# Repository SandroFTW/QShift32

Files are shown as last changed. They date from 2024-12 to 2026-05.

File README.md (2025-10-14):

# QShift32 - ESP32 based timing retard quickshifter module for motorcycles
This project is basically a new revision of my other project "quickshiftuino".
The differences are pretty big though, so I decided to create a new repository.

"**quickshiftuino**" had 2 channels that could cut the power to the ignition coils on the high side (P-Mos).
That topology works great, is fairly simple and reliable, but doesn't allow for more complex features.

"**QShift32**" uses all the thoroughly tested sub-circuits of "quickshiftuino" except the power switching components.
It instead offers 4 independent channels switched by IGBTs on the low side.
They can withstand high voltages and high current and are configured to pull down the low side of the ignition coil.
This can either be used to fully prevent sparks from firing or delay them by a precise time to achieve an ignition retard.

[**Demonstration Video**](https://www.youtube.com/watch?v=TwFzDqyh4EY)

[**Latest feature development: staggered cut**](https://youtu.be/_X9n1uwMxqk)

R1 PCB 3D model:

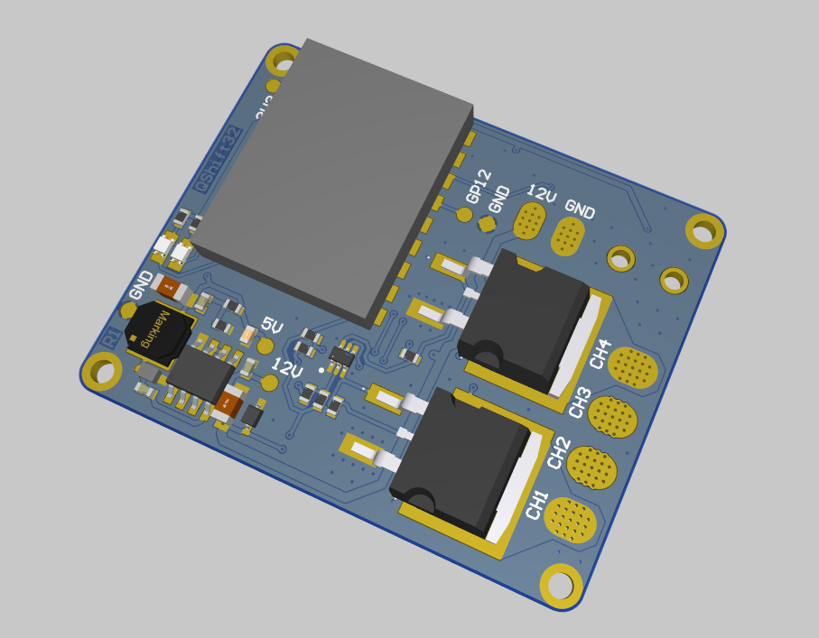
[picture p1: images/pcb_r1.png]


## New possibilities
- Either ignition timing retard or full spark cut to allow clutchless shifting
- Ignition timing retard will smoothly go back to normal operation after shift is done (no jerky movement, less gearbox wear)
- Smooth control over engine power transitions -> extremely smooth shifts (upshifts while leaning and accelerating possible)
- RPM measurement even during power cut (not during full spark cut, only ignition retard)
- During upshift period fuel gets ignited in the exhaust instead of remaining unburnt (controllable pops and flame strength)
- Pit limiter and launch control (RPM limiter) with spark cut and ignition retard (soft limiter or hard limiter with pops and flames)
- Precise dwell time and time per revolution measurement for each channel (1 µs precision)
- Expandable to support handlebar buttons, gear indicator, shift light (not implemented yet), etc.

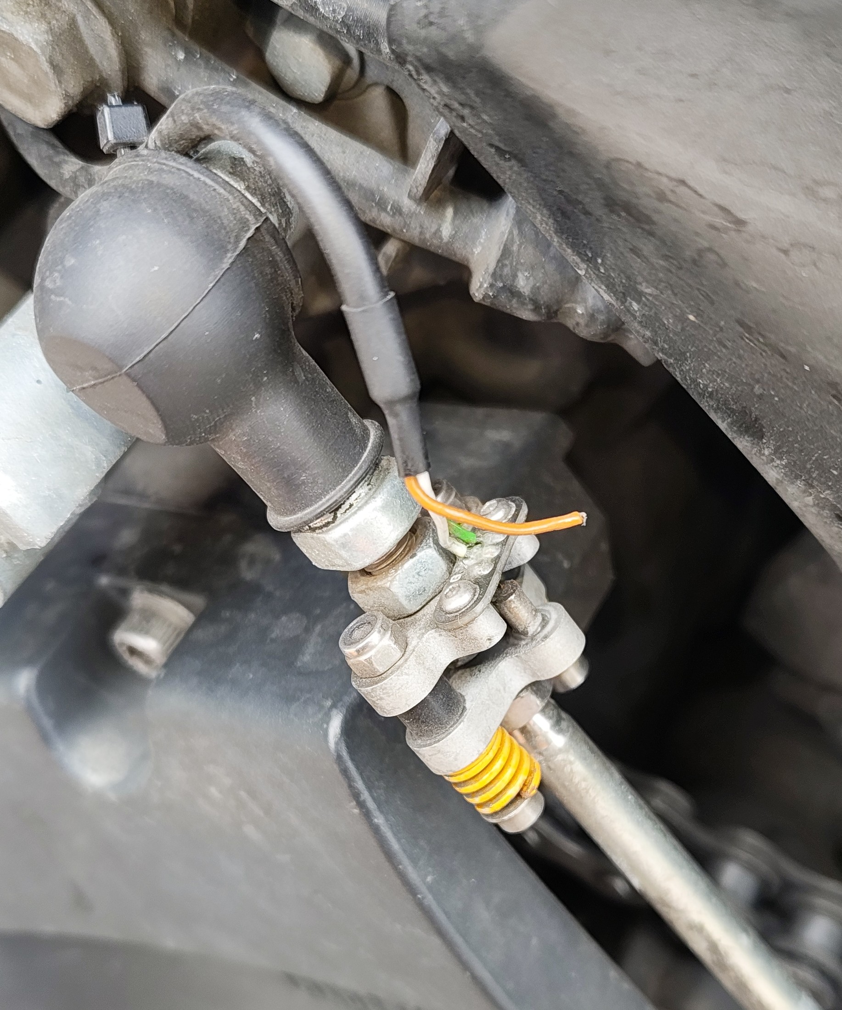
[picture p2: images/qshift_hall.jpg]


My DIY hall based pressure sensor with CNC aluminium parts and 3d printed hotbed springs (die cast springs)
(Ignore the broken wire please ;) )

## Easy configuration
Use any smartphone to connect to the WiFi Access Point opened by QShift32.
IP Adress 192.168.4.1 shows the configuration options.
192.168.4.1/debug.html shows a few internal debug values that can help setting up the config and finding possible errors (mostly needed for development).

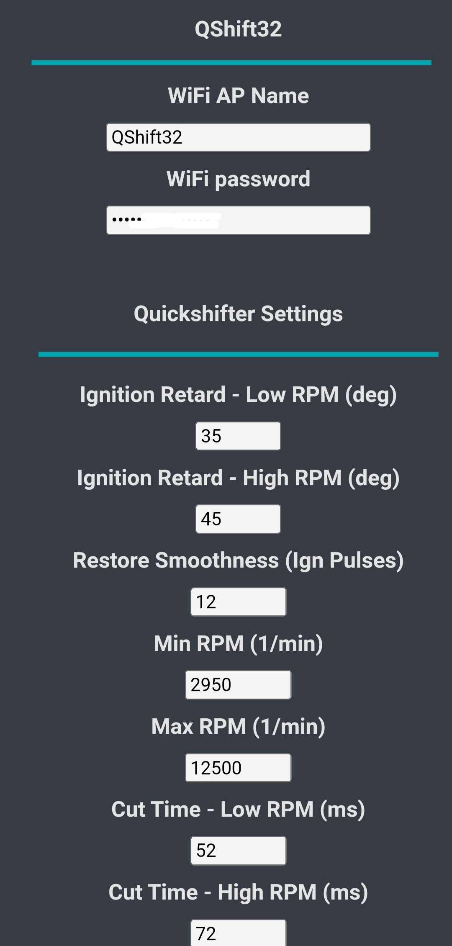
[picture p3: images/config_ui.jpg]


## Precise control over ignition coils
The **bottom graph** shows an unmodified reference ignition coil signal as produced by the engine ECU.

The **top graph** shows the modified ignition pulse, controlled by QShift32.
It prevents ignition pulses for a set time and then slowly reintroduces engine power output by ramping down the ignition retard angle.

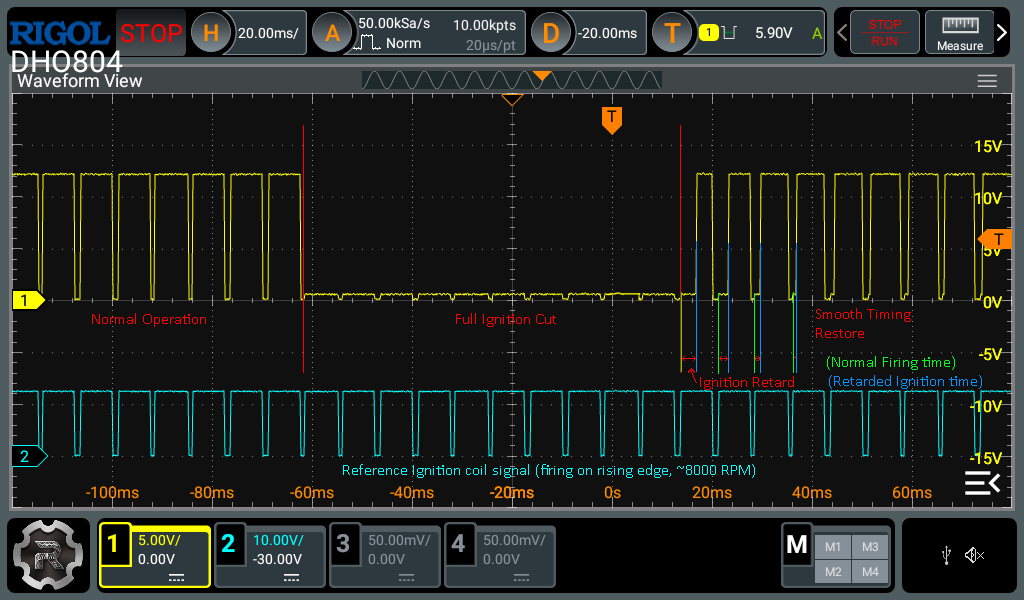
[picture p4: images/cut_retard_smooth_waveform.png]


## Next steps (high to low priority)
- Upload more pictures and write easy-to-follow build instructions and documentation
- Improve code structure, efficiency and write more code documentation
- Try to reduce the amount of configuration options for simplicity
- Find a way to reliably measure variable reluctance wheel speed sensors (only 0-5V hall type working right now)
- Design a case that holds the PCB and connectors (ideally somewhat water splash proof)
- Find a way of controlling multiple channels simultaneously with a single timer (very low priority)

The pulse measurement and IGBT switching schematic and some parts of the code were inspired by the "DIY Quickshifter" series by Gil Vargas on YouTube.
He explains all the steps in great detail.

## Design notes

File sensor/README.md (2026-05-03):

PCB Order settings:
2 layers, 1mm thickness, 1oz copper

CNC parts settings:
threads: yes, meterial: aluminium 7075, surface: bead blasted
(not that important to do it exactly like this)

metal parts + PCBs should be <30€ if ordered from JLCPCB

I used small 3x10mm cylindrical neodymium magnets (only one piece needed) and yellow 3d printer hotbed springs (die cast springs) in 8mm OD, 4.5mm ID, 10mm length (~8kg each for full compression)

The hall sensor PCB needs a single 1uF 0603 capacitor and DRV5057A3EDBZRQ1 SMD hall sensor. It outputs a PWM signal that gets filtered on the QShift32 PCB.

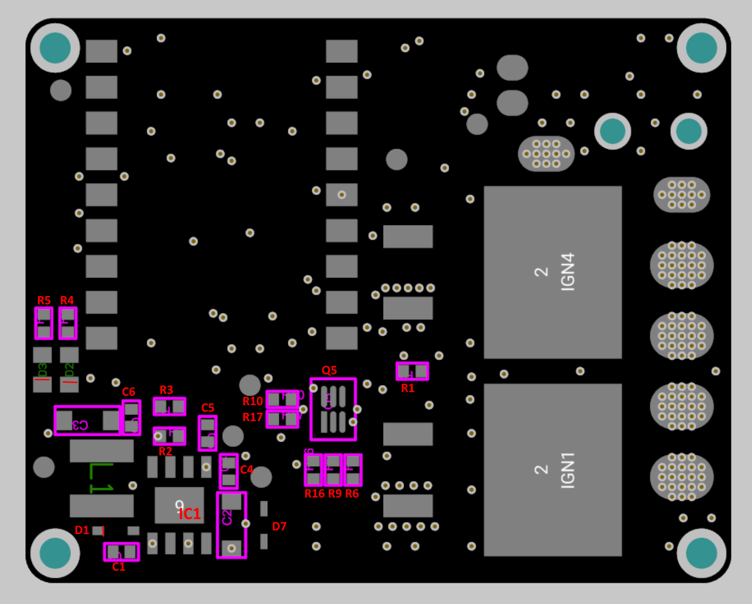
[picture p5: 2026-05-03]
pcb/Top_designators.png

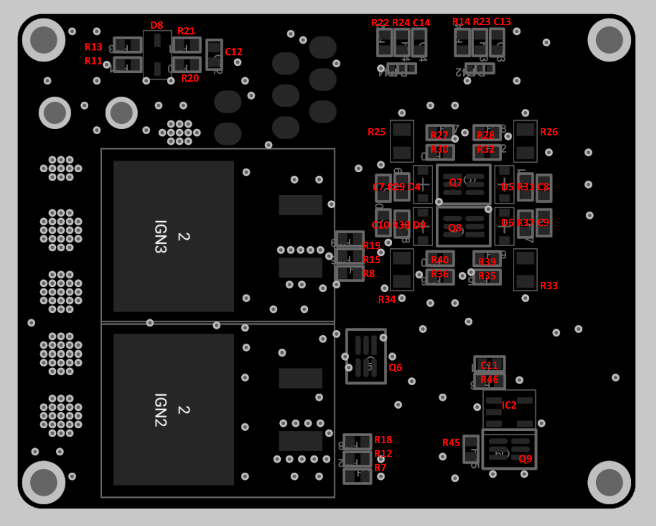
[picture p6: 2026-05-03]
pcb/Bottom_designators.png

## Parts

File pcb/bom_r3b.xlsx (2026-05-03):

Name | Description | Designator | Quantity
C0603C104K3PACTU | C0603 0.10 μF X5R 30ppm/°C 10.00% 25 V | C1, C4, C6 | 3
C3216X5R1E476M160AC | Multilayer Ceramic Capacitors 47uF ±20% 25V X5R SMD 1206 | C2, C3 | 2
C0603C225K4PACTU | CAP CER 2.2UF 16V X5R 0603 | C5 | 1
C0603C333K1RECAUTO | C0603C333K1RECAUTO 0603 (1608METRIC) Ceramic Capacitor Esd SMD Auto X7R 100V 0.033MUF ±10% X7R | C7, C8, C9, C10 | 4
C0603C103K5RACTU | CAP CER 10000PF 50V X7R 0603 | C11 | 1
C0603C473K3RACTU | CAP CER 0.047UF 25V 10% X7R 0603 | C12 | 1
CL10A105KA8NNNC | Cap Ceramic 1uF 25V X5R ±10% Pad SMD 0603 +85°C T/R | C13, C14 | 2
BAT165 | Medium Power AF Schottky Diode, SOD323, Reel, Green | D1 | 1
150080RS75000 |  | D2 | 1
150080GS75000 |  | D3 | 1
SZMM3Z4V7T1G | Zener Voltage Regulator, 300 mW, 2-Pin SOD-323, Pb-Free, Tape and Reel | D4, D5, D6, D9 | 4
D20V0L1B2WS-7 | TVS Diode (Bi-directional) | D7, D8 | 2
MP9486GN-Z | Integrated Circuit | IC1 | 1
74HC1G14GV,125 | Integrated Circuit | IC2 | 1
Waveshare ESP32-S3 Mini | WaveShare ESP32-S3 Mini Development Board ESP32-S3FH4R2 240MHz 2.4GHz Wi-Fi Bluetooth 5 | IC4 | 1
74404052470 | 74404052470 Inductors, Fixed, WE-LQS SMD 5020 47uH 0.8A 521mOhms | L1 | 1
STGB20M65DF2 | Transistor IGBT | Q1, Q2, Q3, Q4 | 4
DMN3190LDW-7 | MOSFET 2N-CH 30V 1A SOT363 | Q5, Q6, Q7, Q8, Q9 | 5
CRCW06033K30FKEA | RES Thick Film, 3.3kΩ, 1%, 0.1W, 100ppm/°C, 0603 | R1, R6, R7, R8, R14, R22 | 6
CRCW060310K0FKEC | RES Thick Film, 10kΩ, 1%, 0.1W, 100ppm/°C, 0603 | R2, R9, R10, R11, R12, R13, R15, R21, R27, R28, R30, R32, R35, R36, R39, R40, R45 | 17
CRCW0603240KFKEA | RES Thick Film, 240kΩ, 1%, 0.1W, 100ppm/°C, 0603 | R3 | 1
CRCW0603100RFKEB | RES Thick Film, 100Ω, 1%, 0.1W, 100ppm/°C, 0603 | R4, R5 | 2
CRCW06031K00FKEA | RES Thick Film, 1kΩ, 1%, 0.1W, 100ppm/°C, 0603 | R16, R17, R18, R19 | 4
CRCW06032M00FKEA | RES Thick Film, 2MΩ, 1%, 0.1W, 100ppm/°C, 0603 | R20 | 1
CRCW060320K0FKEA | RES Thick Film, 20kΩ, 1%, 0.1W, 100ppm/°C, 0603 | R23, R24 | 2
SDR10EZPJ103 | Resistor | R25, R26, R33, R34 | 4
CRCW06033K00FKEA | RES Thick Film, 3kΩ, 1%, 0.1W, 100ppm/°C, 0603 | R29, R31, R37, R38 | 4
CRCW04020000Z0ED | RES Thick Film, 0Ω, 0.063W, 0402 | R41, R42, R43, R44 | 4
CRCW06032K20FKEC | RES Thick Film, 2.2kΩ, 1%, 0.1W, 100ppm/°C, 0603 | R46 | 1

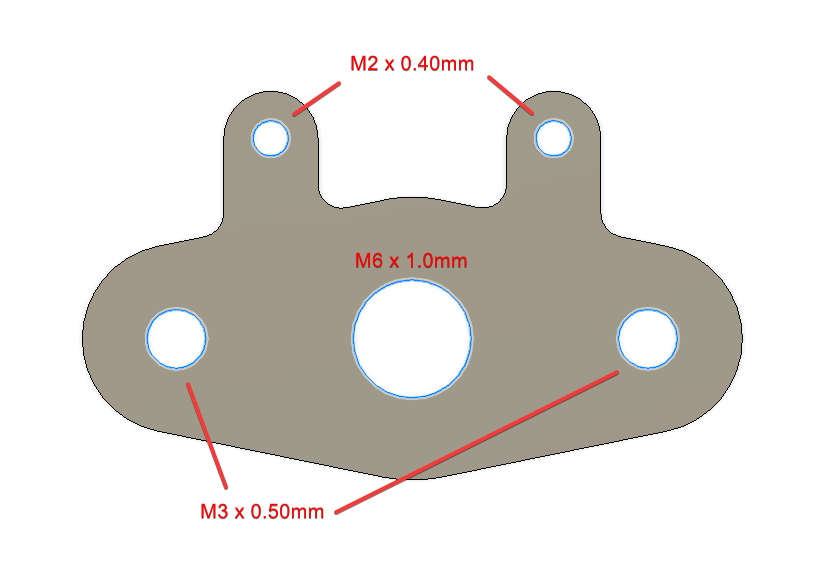
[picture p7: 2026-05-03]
sensor/metal parts/sensor mount threads.png

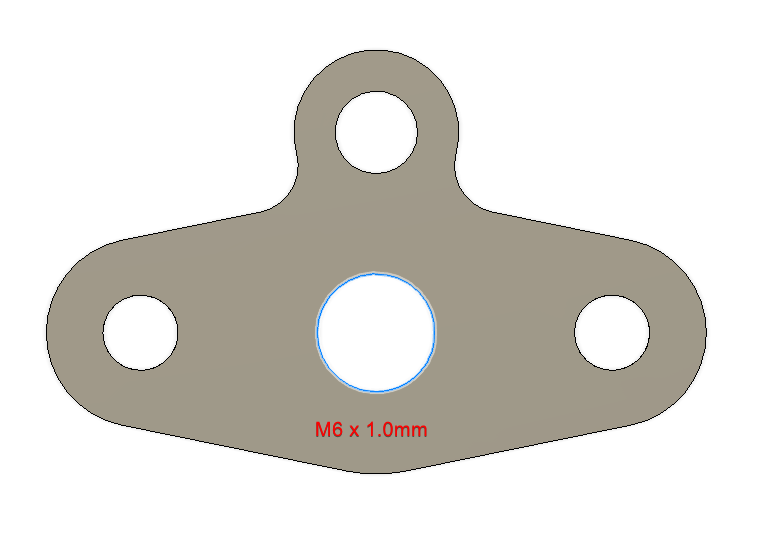
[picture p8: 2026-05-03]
sensor/metal parts/magnet mount threads.png

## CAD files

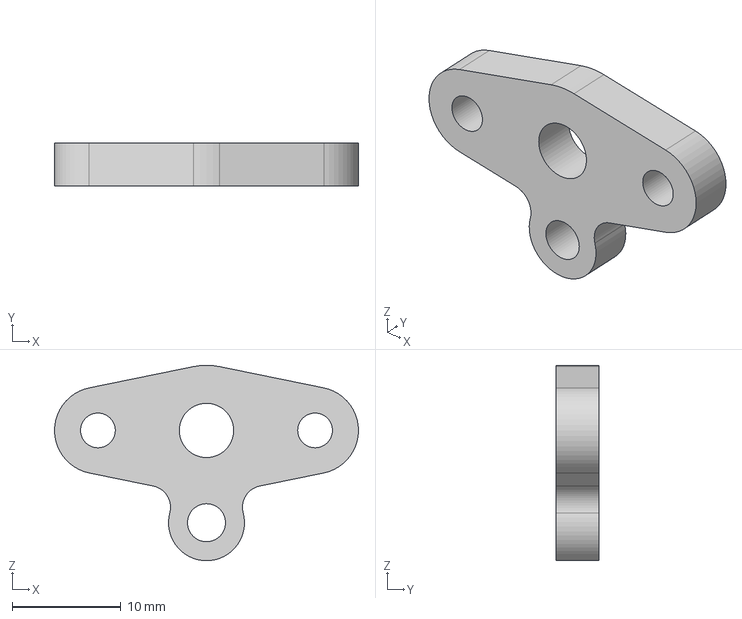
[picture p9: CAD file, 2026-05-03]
sensor/metal parts/magnet mount.step
28.0 x 4.00 x 18.0 mm

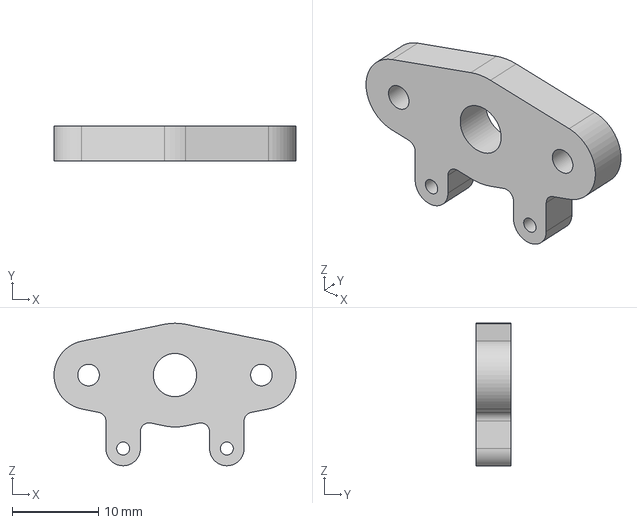
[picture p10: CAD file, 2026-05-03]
sensor/metal parts/sensor mount.step
28.0 x 4.00 x 16.5 mm

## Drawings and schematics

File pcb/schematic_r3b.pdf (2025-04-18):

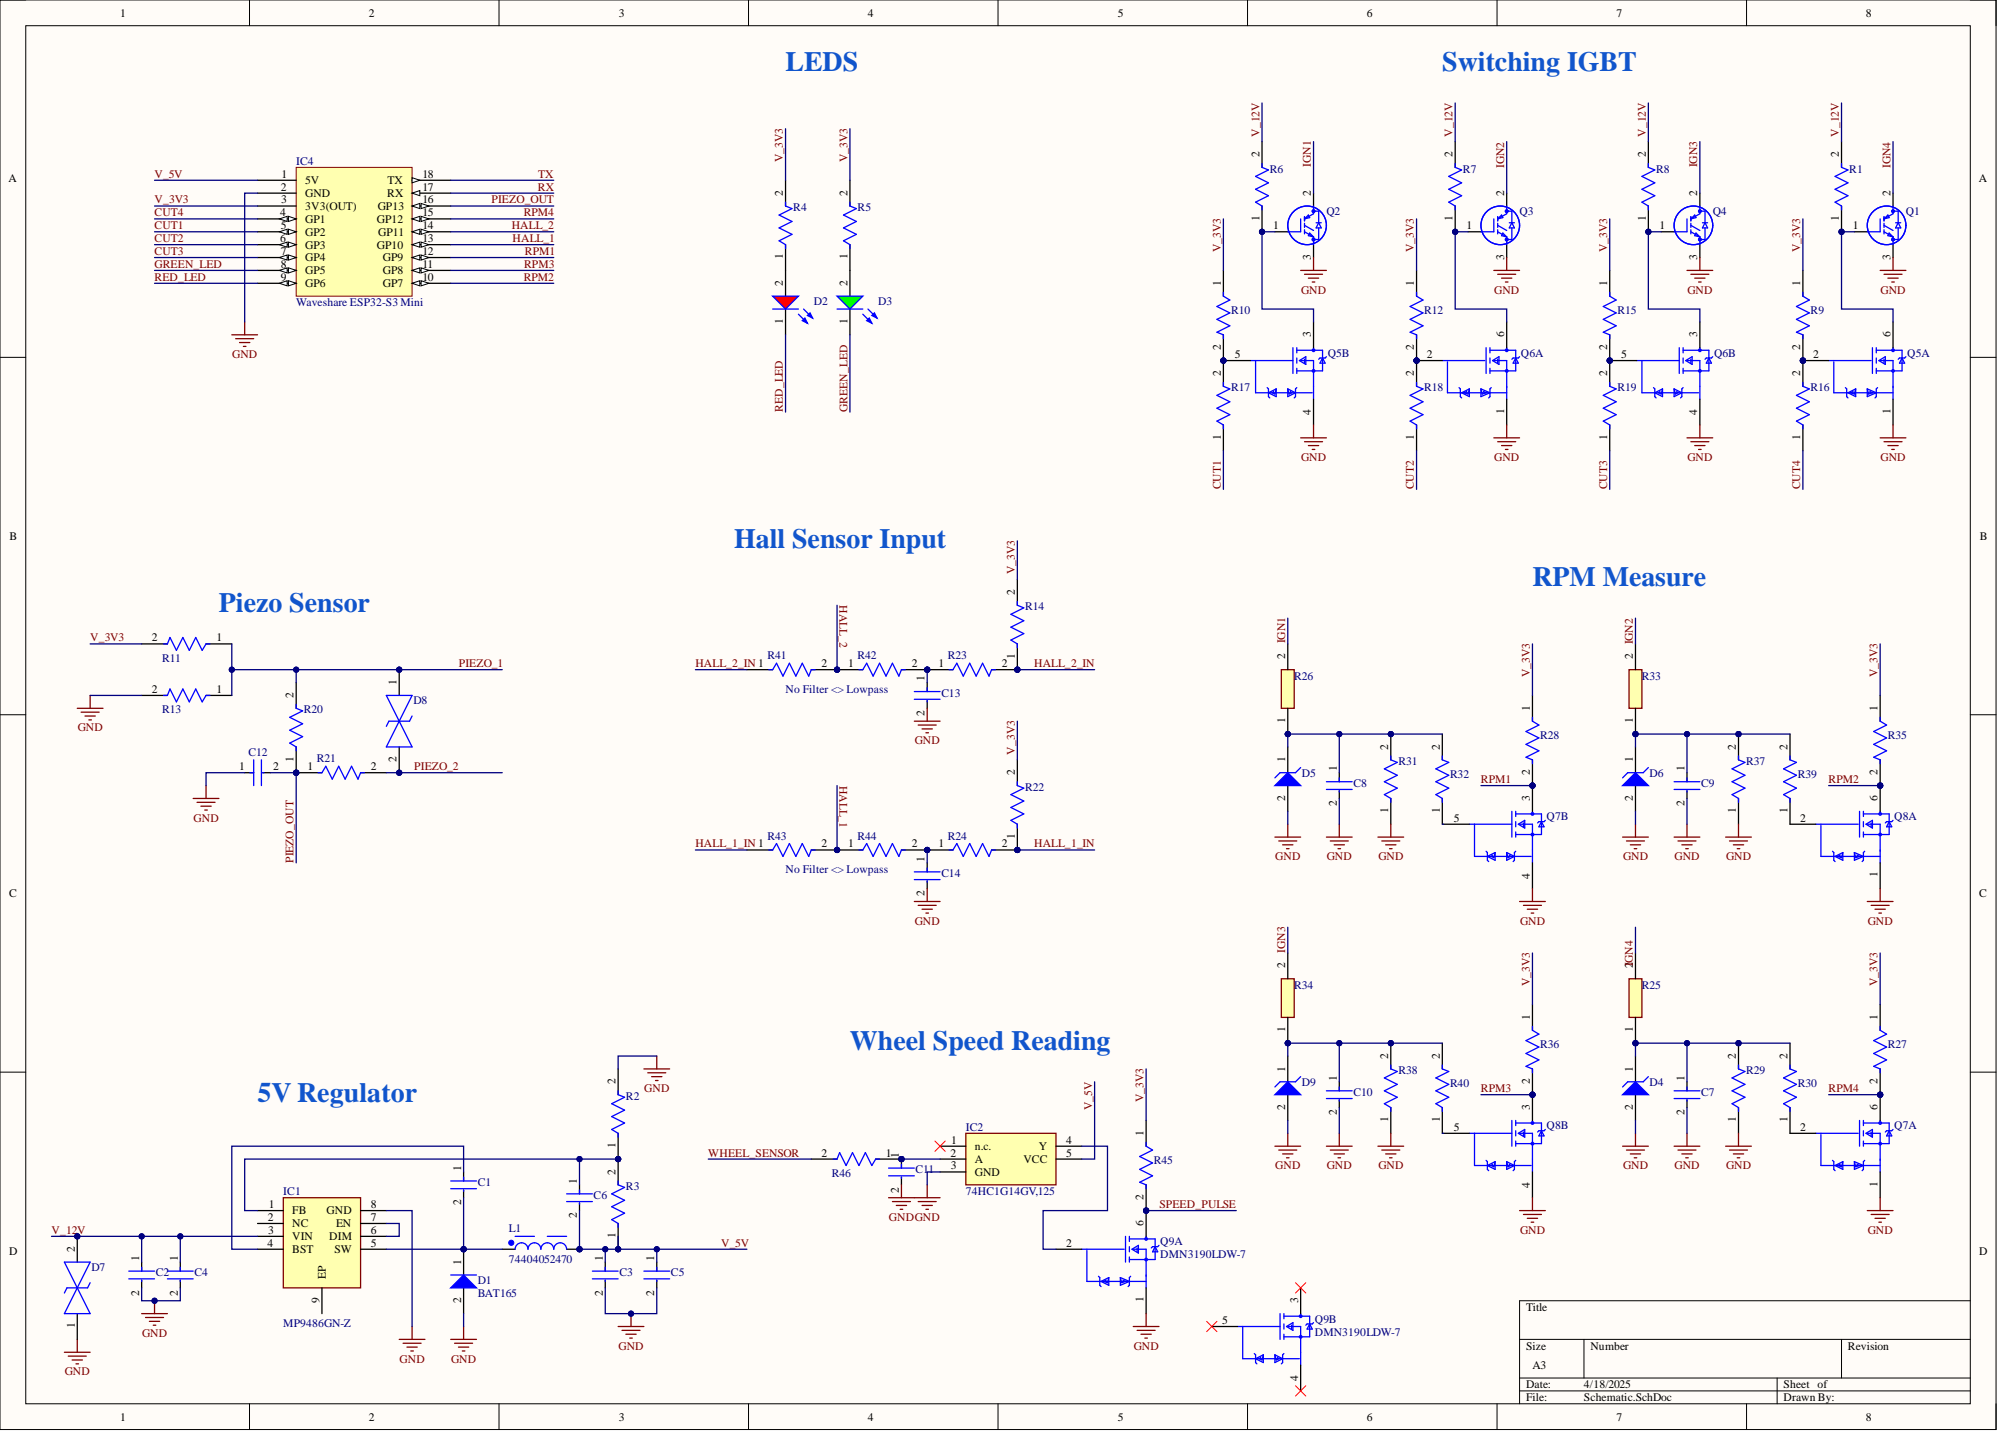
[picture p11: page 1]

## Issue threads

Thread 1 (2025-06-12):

Question: Are there planned changes to the PCB design?

Tury991, 2025-06-12:
Hello @SandroFTW,

First of all, thank you very much! Really good project!
I am interested in building the project and want to try making my own version of the hall sensor. Before I begin, I wanted to ask if you have any plans to make changes to the PCB in the near future. This information will help me decide the right time to start.

Thank you!

Closed 2025-06-23.

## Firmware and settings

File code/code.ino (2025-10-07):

/* TODO:
  - Maybe add some kind of detection for cylinder count (of course only while engine is running) so cfg.restore gets scaled accordingly (makes config more generally usable)
  - Rewrite so each Channel doesn't need its own timer
    -> meh, semi fixed by removing the need for a seperate timekeeping timer so all 4 timers can be used for qs channels
  - Implement volatile unsigned long lowStartTime[4] -> Prevent coils from overheating because of extended dwell time > ~200ms
  - Think how cfg.restore is affected by cylinder/coil count with wasted spark (double the cylinder count needs double cfg.restore for same smoothness, change to float for more precision or unnecessary?)
  - Rename cfg.wastedSpark to something that describes it better (crank degrees per ignition pulse per coil) (Change back to boolean, create global variable that stores 360 or 720 for coilInterrupt function but keeps this simple)
  - Try to improve performance of coilInterrupt interrupt function (is micros() bad? less calculations)
  - Make currRetard calculation logarithmic instead of linear (more change at low rpm, less change at high rpm, with configurable breakpoint percentage, maybe see throttle expo in betaflight)
*/

#include <WebSocketsServer.h>
#include <ESPAsyncWebServer.h>
#include <AsyncWebConfig.h>
#include <esp_wifi.h>
#include <AsyncTCP.h>
#include <SPIFFS.h>
#include <WiFi.h>

#include <Arduino.h>

#include "soc/gpio_struct.h"
#include "soc/gpio_reg.h"
#include "driver/gpio.h"

WebSocketsServer webSocket = WebSocketsServer(81);

// Global variables
volatile unsigned long currTime          = 0;     // current timestamp in 1 µs steps (1 MHz)
volatile unsigned long speedPulses       = 0;     // Pulse count from the wheel speed sensor in the last interval (500 ms / 2 Hz)
volatile unsigned long dwellBeginTime[4] = {0};   // time of last dwell start in µs steps
volatile unsigned long lastDwellTime[4]  = {0};   // duration of last dwell pulse in µs steps
volatile unsigned long lastRPMdelta[4]   = {0};   // Stores time bewteen two ignition pulses, needed for RPM calculation
volatile bool lastMeasureState[4]        = {0};   // last state of the filtered coil state input
volatile bool shiftingTrig               = false; // Controls whether ignition is retarded
volatile bool limitingRPM                = false; // Temporarily changes restore time to 999 while RPM limiting
volatile int currRetard                  = 0;     // Used for gradual ignition retard recovery to normal operation
volatile int currRestore                 = 0;     // Calculated deg/ignition pulse recovery speed

unsigned long lastCycle           = 0;     // When was the last main loop cycle (1 kHz)
unsigned long lastRead            = 0;     // When was the last ADC sensor reading (20 Hz)
unsigned long lastCut             = 0;     // When was the last ignition cut/retard begin
unsigned long lastSpeedRead       = 0;     // When was the last rear wheel speed measurement (2 Hz)

int currHoldTime                  = 0;     // Interpolated hold time based on current RPM and low/high time
int lastRPM                       = 0;
int lastWheelRPM                  = 0;     // Measured rear wheel speed (1/min)
float lastWheelSpeed              = 0;     // Calculated rear wheel speed (km/h)
int pressureValue                 = 0;     // Piezo/Hall sensor pressure value
int limiterState                  = 0;     // Current state of RPM limiter mode
bool buttonPressed                = false; // Handlebar button state
bool lastButtonState              = false; // Last button state for edge detection
bool waitHyst                     = true;  // Needs to be low before another upshift is allowed

// Timer instances
hw_timer_t *t_cut[4]  = {NULL, NULL, NULL, NULL};

// Pin definitions
const int HALL_PINS[2]    = {10, 11};
const int IGBT_PINS[4]    = {2, 3, 4, 1};
const int MEASURE_PINS[4] = {9, 14, 7, 8}; // Handwired first revision (xj6)
//const int MEASURE_PINS[4] = {9, 7, 8, 12}; // PCB Design Pins (grom, R3b)

const int WHEEL_PIN = 15; // 12 on my grom, 15 on my xj6, 14 in R3b PCB revision
const int PIEZO_PIN = 13;
const int GREEN_PIN = 5;
const int RED_PIN   = 6;

enum lim {
  OFF = 0,
  LAUNCH = 1,
  PIT = 2
};

String params = "["
  "{"
  "'name':'password',"
  "'label':'WiFi password',"
  "'type':"+String(INPUTPASSWORD)+","
  "'default':''"
  "},"
  "{"
  "'name':'category1',"
  "'label':'Quickshifter Settings',"
  "'type':"+String(CATEGORY)+""
  "},"
  "{"
  "'name':'retardLow',"
  "'label':'Ignition Retard - Low RPM (deg)',"
  "'type':"+String(INPUTNUMBER)+","
  "'min':0,'max':180,"
  "'default':'40'"
  "},"
  "{"
  "'name':'retardHigh',"
  "'label':'Ignition Retard - High RPM (deg)',"
  "'type':"+String(INPUTNUMBER)+","
  "'min':0,'max':180,"
  "'default':'60'"
  "},"
  "{"
  "'name':'restore',"
  "'label':'Restore Smoothness (Ign Pulses)',"
  "'type':"+String(INPUTNUMBER)+","
  "'min':0,'max':1000,"
  "'default':'20'"
  "},"
  "{"
  "'name':'minRPM',"
  "'label':'Min RPM (1/min)',"
  "'type':"+String(INPUTNUMBER)+","
  "'min':1000,'max':20000,"
  "'default':'2900'"
  "},"
  "{"
  "'name':'maxRPM',"
  "'label':'Max RPM (1/min)',"
  "'type':"+String(INPUTNUMBER)+","
  "'min':2000,'max':20000,"
  "'default':'12500'"
  "},"
  "{"
  "'name':'holdTimeLow',"
  "'label':'Cut Time - Low RPM (ms)',"
  "'type':"+String(INPUTNUMBER)+","
  "'min':1,'max':1000,"
  "'default':'49'"
  "},"
  "{"
  "'name':'holdTimeHigh',"
  "'label':'Cut Time - High RPM (ms)',"
  "'type':"+String(INPUTNUMBER)+","
  "'min':1,'max':1000,"
  "'default':'72'"
  "},"
  "{"
  "'name':'deadTime',"
  "'label':'Dead Time (ms)',"
  "'type':"+String(INPUTNUMBER)+","
  "'min':1,'max':5000,"
  "'default':'300'"
  "},"
  "{"
  "'name':'cutSens',"
  "'label':'Cut Sensitivity (1-4095)',"
  "'type':"+String(INPUTNUMBER)+","
  "'min':1,'max':5000,"
  "'default':'1000'"
  "},"
  "{"
  "'name':'cutHyst',"
  "'label':'Cut Hysteresis (1-4095)',"
  "'type':"+String(INPUTNUMBER)+","
  "'min':1,'max':5000,"
  "'default':'500'"
  "},"
  "{"
  "'name':'fullCut',"
  "'label':'Full Ignition Cut',"
  "'type':"+String(INPUTCHECKBOX)+","
  "'default':'1'"
  "},"
  "{"
  "'name':'wastedSpark',"
  "'label':'Wasted Spark Setup',"
  "'type':"+String(INPUTCHECKBOX)+","
  "'default':'1'"
  "},"
  "{"
  "'name':'category2',"
  "'label':'2-Step RPM Limiter',"
  "'type':"+String(CATEGORY)+""
  "},"
  "{"
  "'name':'limiterAlways',"
  "'label':'Limiter Always Active',"
  "'type':"+String(INPUTCHECKBOX)+","
  "'default':'1'"
  "},"
  "{"
  "'name':'limiterFullCut',"
  "'label':'Limiter Full Cut',"
  "'type':"+String(INPUTCHECKBOX)+","
  "'default':'0'"
  "},"
  "{"
  "'name':'limiterRPM',"
  "'label':'Limiter RPM (1/min)',"
  "'type':"+String(INPUTNUMBER)+","
  "'min':0,'max':20000,"
  "'default':'3600'"
  "},"
  "{"
  "'name':'launchRPM',"
  "'label':'Launch Control RPM (1/min)',"
  "'type':"+String(INPUTNUMBER)+","
  "'min':0,'max':20000,"
  "'default':'2500'"
  "},"
  "{"
  "'name':'limiterCut',"
  "'label':'Limiter Cut Gain (ms/100rpm)',"
  "'type':"+String(INPUTNUMBER)+","
  "'min':1,'max':1000,"
  "'default':'10'"
  "},"
  "{"
  "'name':'limiterRetard',"
  "'label':'Limiter Retard (deg)',"
  "'type':"+String(INPUTNUMBER)+","
  "'min':0,'max':180,"
  "'default':'30'"
  "},"
  "{"
  "'name':'limiterDiv',"
  "'label':'Limiter Restore Divisor',"
  "'type':"+String(INPUTNUMBER)+","
  "'min':1,'max':20,"
  "'default':'1'"
  "},"
  "{"
  "'name':'limiterMaxSpeed',"
  "'label':'Limiter Max Speed (km/h)',"
  "'type':"+String(INPUTNUMBER)+","
  "'min':0,'max':1000,"
  "'default':'15'"
  "},"
  "{"
  "'name':'category3',"
  "'label':'Misc Options',"
  "'type':"+String(CATEGORY)+""
  "},"
  "{"
  "'name':'pressureInput',"
  "'label':'Pressure Sensor Input',"
  "'type':"+String(INPUTSELECT)+","
  "'options':["
  "{'v':'0','l':'Piezo'},"
  "{'v':'1','l':'ADC 1'},"
  "{'v':'2','l':'ADC 2'}],"
  "'default':'1'"
  "},"
  "{"
  "'name':'buttonInput',"
  "'label':'Button Input',"
  "'type':"+String(INPUTSELECT)+","
  "'options':["
  "{'v':'0','l':'None'},"
  "{'v':'1','l':'ADC 1'},"
  "{'v':'2','l':'ADC 2'}],"
  "'default':'0'"
  "},"
  "{"
  "'name':'wheelSensor',"
  "'label':'Wheel Speed Sensor',"
  "'type':"+String(INPUTCHECKBOX)+","
  "'default':'0'"
  "},"
  "{"
  "'name':'speedScale',"
  "'label':'Wheel Circumference (mm)',"
  "'type':"+String(INPUTNUMBER)+","
  "'min':1,'max':20000,"
  "'default':'1528'"                             // Grom 15/34 (Sprocket) * 1529 (Wheel Dia mm) = 675 (Distance per rear wheel rev)
  "},"
  "{"
  "'name':'sensorPulses',"
  "'label':'Pulses per Wheel Revolution',"
  "'type':"+String(INPUTNUMBER)+","
  "'min':1,'max':1000,"
  "'default':'70'"
  "}"
  "]";

AsyncWebServer server(80);
AsyncWebConfig conf;

struct cfgOptions
{
  char ssid[32];
  char password[32];

  int retardLow;
  int retardHigh;
  int restore;

  int minRPM;
  int maxRPM;

  int holdTimeLow;
  int holdTimeHigh;

  int deadTime;
  int cutSens;
  int cutHyst;

  bool fullCut;
  float wastedSpark;

  bool limiterAlways;
  bool limiterFullCut;
  int limiterRPM;
  int launchRPM;
  int limiterCut;
  int limiterRetard;
  int limiterDiv;
  int limiterMaxSpeed;

  int pressureInput;
  int buttonInput;
  bool wheelSensor;
  int speedScale;
  int sensorPulses;
} cfg;

void transferWebconfToStruct(String results)
{
  cfg.retardLow = conf.getInt("retardLow");
  cfg.retardHigh = conf.getInt("retardHigh"); 
  cfg.restore = conf.getInt("restore");

  cfg.minRPM = conf.getInt("minRPM");
  cfg.maxRPM = conf.getInt("maxRPM");

  cfg.holdTimeLow = conf.getInt("holdTimeLow");
  cfg.holdTimeHigh = conf.getInt("holdTimeHigh");

  cfg.deadTime = conf.getInt("deadTime");
  cfg.cutSens = conf.getInt("cutSens");
  cfg.cutHyst = conf.getInt("cutHyst");

  cfg.fullCut = conf.getBool("fullCut");
  cfg.wastedSpark = conf.getBool("wastedSpark") ? 360.f : 720.f;

  cfg.limiterAlways = conf.getBool("limiterAlways");
  cfg.limiterFullCut = conf.getBool("limiterFullCut");
  cfg.limiterRPM = conf.getInt("limiterRPM");
  cfg.launchRPM = conf.getInt("launchRPM");
  cfg.limiterCut = conf.getInt("limiterCut");
  cfg.limiterRetard = conf.getInt("limiterRetard");
  cfg.limiterDiv = conf.getInt("limiterDiv");
  cfg.limiterMaxSpeed = conf.getInt("limiterMaxSpeed");

  String pres = conf.getString("pressureInput").c_str();
  String butt = conf.getString("buttonInput").c_str();

  if (pres == "0")
    cfg.pressureInput = 0; // Piezo
  else if (pres == "1")
    cfg.pressureInput = 1; // ADC 1
  else if (pres == "2")
    cfg.pressureInput = 2; // ADC 2

  if (butt == "0")
    cfg.buttonInput = 0; // None
  else if (butt == "1")
    cfg.buttonInput = 1; // ADC 1
  else if (butt == "2")
    cfg.buttonInput = 2; // ADC 2

  cfg.wheelSensor = conf.getInt("wheelSensor");
  cfg.speedScale = conf.getInt("speedScale");
  cfg.sensorPulses = conf.getInt("sensorPulses");
}

const char debug_html[] PROGMEM = R"rawliteral(
<!DOCTYPE html>
<html lang="en">
<head>
  <meta charset="UTF-8">
  <meta name="viewport" content="width=device-width, initial-scale=1.0">
  <title>QShift32 Debug</title>
</head>
<body>
  <h2>QShift32 Debug</h2>
  <p id="val1">...</p>
  <p id="val2">...</p>
  <p id="val3">...</p>
  <p id="val4">...</p>
  <p id="val5">...</p>
  <p id="val6">...</p>
  <br>
  <p id="val7">...</p>
  <p id="val8">...</p>
  <script>
    const valEl1 = document.getElementById('val1');
    const valEl2 = document.getElementById('val2');
    const valEl3 = document.getElementById('val3');
    const valEl4 = document.getElementById('val4');
    const valEl5 = document.getElementById('val5');
    const valEl6 = document.getElementById('val6');
    const valEl7 = document.getElementById('val7');
    const valEl8 = document.getElementById('val8');
    const ws = new WebSocket(`ws://${location.hostname}:81/`);

    ws.onmessage = function(event) {
      const [val1, val2, val3, val4, val5, val6, val7, val8] = event.data.split(",");
      valEl1.innerText = `Pressure: ${val1}`;
      valEl2.innerText = `RPM: ${val2}`;
      valEl3.innerText = `RPM change: ${val3}`;
      valEl4.innerText = `targetRetard: ${val4}`;
      valEl5.innerText = `currHoldTime: ${val5}`;
      valEl6.innerText = `currRestore: ${val6}`;
      valEl7.innerText = `Speed (km/h): ${val7}`;
      valEl8.innerText = `Limiter Mode: ${val8}`;
    };
  </script>
</body>
</html>
)rawliteral";

void handleRoot(AsyncWebServerRequest *request)
{
  conf.handleFormRequest(request);
}

// Create a task that will be executed on Core 0 (instead of 1)
TaskHandle_t Task1;
void push_debug(void *parameters)
{
  for (;;)
  {
    //String sTrig = shiftingTrig ? "true" : "false";
    String lMode = limiterState == OFF ? "OFF" : (limiterState == PIT ? "PIT" : (limiterState == LAUNCH ? "LAUNCH" : "error"));

    String broadcastString = String(pressureValue) +                "," + String(lastRPM) +       "," + String(lastRPMdelta[0]) + ","
                           + String(currRetard) +                "," + String(currHoldTime) +  "," + String(currRestore) + ","
                           + String(lastWheelSpeed) +            "," + lMode;

    webSocket.loop();
    webSocket.broadcastTXT(broadcastString);

    delay(200);
  }
}



// Gets executed when (lastDwell + calculated delay) passed after shifting
void IRAM_ATTR on_t0_cut()
{
  // digitalWrite(IGBT_PINS[0], HIGH);
  GPIO.out_w1ts = (1 << IGBT_PINS[0]);
}
void IRAM_ATTR on_t1_cut()
{
  // digitalWrite(IGBT_PINS[1], HIGH);
  GPIO.out_w1ts = (1 << IGBT_PINS[1]);
}
void IRAM_ATTR on_t2_cut()
{
  // digitalWrite(IGBT_PINS[2], HIGH);
  GPIO.out_w1ts = (1 <<IGBT_PINS[2]);
}
void IRAM_ATTR on_t3_cut()
{
  // digitalWrite(IGBT_PINS[3], HIGH);
  GPIO.out_w1ts = (1 << IGBT_PINS[3]);
}

// When ECU changes state of coil (pull low or release)
void coilInterrupt(int ch)
{
  bool bPin = digitalRead(MEASURE_PINS[ch]); // Measurement Pin
  unsigned long lTime = micros();

  // When ECU pulls coil to ground (rising edge on logic signal)
  if (bPin && !lastMeasureState[ch])
  {
    lastRPMdelta[ch] = lTime - dwellBeginTime[ch];

    unsigned long delayForRetard = (currRetard / cfg.wastedSpark) * (lTime - dwellBeginTime[ch]);

    if (!shiftingTrig && currRetard > 0) {
      currRetard = max(0, currRetard - currRestore);
    }

    dwellBeginTime[ch] = lTime;

    // Either actively retarding ignition or recovering
    if (currRetard > 0)
    {
      if (shiftingTrig && cfg.fullCut)
      {
        delayForRetard += ((currHoldTime*1000 / lastRPMdelta[ch]) + 1) * lastRPMdelta[ch];
        shiftingTrig = false;
      }

      // digitalWrite(IGBT_PINS[ch], LOW); // Close IGBT
      GPIO.out_w1tc = (1 << IGBT_PINS[ch]);
      timerWrite(t_cut[ch], 0);
      timerAlarm(t_cut[ch], lastDwellTime[ch] + delayForRetard, false, 0);
    }
  }
  // When ECU releases coil (falling edge on logic signal)
  else if (!bPin && !shiftingTrig && currRetard == 0 && dwellBeginTime[ch])
  {
    lastDwellTime[ch] = lTime - dwellBeginTime[ch];
  }

  lastMeasureState[ch] = bPin;
}

void IRAM_ATTR onPC0() { coilInterrupt(0); }
void IRAM_ATTR onPC1() { coilInterrupt(1); }
void IRAM_ATTR onPC2() { coilInterrupt(2); }
void IRAM_ATTR onPC3() { coilInterrupt(3); }

void IRAM_ATTR onWheelSpeed()
{
  speedPulses++;
}

void setup()
{
  Serial.begin(57600);

  // LED
  pinMode(GREEN_PIN, OUTPUT);
  // digitalWrite(GREEN_PIN, HIGH); // Off default
  GPIO.out_w1ts = (1 << GREEN_PIN);
  pinMode(RED_PIN, OUTPUT);
  // digitalWrite(RED_PIN, HIGH); // Off default
  GPIO.out_w1ts = (1 << RED_PIN);

  // Hall, Piezo
  int adcPins[4] = {HALL_PINS[0], HALL_PINS[1], PIEZO_PIN, WHEEL_PIN};
  for (int i = 0; i < 4; i++) {
    pinMode(adcPins[i], INPUT);
  }

  // Ignition IGBT and measurement (set all 4 channels)
  for (int i = 0; i < 4; i++) {
    pinMode(IGBT_PINS[i], OUTPUT);
    // digitalWrite(IGBT_PINS[i], HIGH); // Open IGBT default
    GPIO.out_w1ts = (1 << IGBT_PINS[i]);

    pinMode(MEASURE_PINS[i], INPUT);
  }

  void (*on_cut_funcs[4])() = {on_t0_cut, on_t1_cut, on_t2_cut, on_t3_cut};
  for (int i = 0; i < 4; i++) {
    t_cut[i] = timerBegin(1000000);
    timerAttachInterrupt(t_cut[i], on_cut_funcs[i]);
  }

  // Attach interrupts to MEASURE_PINS[i]
  void (*pcFuncs[4])() = {onPC0, onPC1, onPC2, onPC3};
  for (int i = 0; i < 4; i++) {
    attachInterrupt(digitalPinToInterrupt(MEASURE_PINS[i]), pcFuncs[i], CHANGE);
  }

  // Rear wheel speed sensing
  attachInterrupt(digitalPinToInterrupt(WHEEL_PIN), onWheelSpeed, RISING);

  conf.setDescription(params);
  conf.readConfig();
  transferWebconfToStruct("");

  WiFi.mode(WIFI_AP);
  WiFi.setTxPower(WIFI_POWER_8_5dBm); // 7 also works (other options: 2, 5, 7, 8.5, 11, 13, 15)
  WiFi.softAP(conf.getApName(), conf.values[0].c_str());

  server.on("/", handleRoot);

  server.on("/debug.html", HTTP_GET, [](AsyncWebServerRequest *request) {
    //request->send(SPIFFS, "/debug.html", "text/html");
    request->send_P(200, "text/html", debug_html);
  });

  conf.registerOnSave(transferWebconfToStruct);

  server.begin();
  webSocket.begin();

  xTaskCreatePinnedToCore(push_debug, "CPU_0", 10000, NULL, 1, &Task1, 0);
}

void loop()
{
  // 1 µs precision (1 MHz)
  currTime = micros();

  // Run every 1 ms (1 kHz)
  if ((currTime - lastCycle) >= 1000)
  {
    // Read ADC sensors every 50 ms (20 Hz)
    if ((currTime - lastRead) >= 50000)
    {
      const int inputs[] = {PIEZO_PIN, HALL_PINS[0], HALL_PINS[1], PIEZO_PIN};

      pressureValue = analogRead(inputs[cfg.pressureInput]);
      if (cfg.pressureInput == 0)
        pressureValue = 4095 - pressureValue;
      
      buttonPressed = cfg.buttonInput ? !digitalRead(inputs[cfg.buttonInput]) : false;

      if (buttonPressed && !lastButtonState)
      {
        switch (limiterState)
        {
          case PIT:    limiterState = OFF; break;
          case LAUNCH: limiterState = OFF; break;

          case OFF:
            if (lastWheelSpeed < cfg.limiterMaxSpeed && cfg.wheelSensor)
              limiterState = LAUNCH;
            else
              limiterState = PIT;
            break;
        }
      }

      if (cfg.limiterAlways)
        limiterState = PIT;                                    // TODO: Possible conflict with decelRetarding

      lastButtonState = buttonPressed;

      if (lastRPMdelta[0] > 0)
      {
        lastRPM = ((cfg.wastedSpark > 700) ? 120000000UL : 60000000UL) / lastRPMdelta[0];
        //lastRPM = (cfg.wastedSpark ? 6000000UL : 12000000UL) / lastRPMdelta[0];
      }

      lastRead = currTime;
    }

    // Read wheel speed every 500 ms (2 Hz)
    if (cfg.wheelSensor && (currTime - lastSpeedRead) >= 500000)
    {
      lastWheelRPM = (int)(speedPulses * (120 / (float)cfg.sensorPulses));
      speedPulses = 0;

      lastWheelSpeed = (lastWheelRPM * cfg.speedScale) / 60000.f;

      lastSpeedRead = currTime;
    }

    if (pressureValue < (cfg.cutSens - cfg.cutHyst))
      waitHyst = false;

    // 2-step launch control
    if ((cfg.launchRPM || cfg.limiterRPM) && cfg.limiterCut && cfg.limiterRetard)
    {
      switch (limiterState)
      {
        case LAUNCH:
          if (lastWheelSpeed > cfg.limiterMaxSpeed)
            limiterState = OFF;

          if (cfg.launchRPM && lastRPM > cfg.launchRPM && !shiftingTrig)
          {
            shiftingTrig = true;
            limitingRPM = true;
            waitHyst = true;
            currRetard = cfg.limiterRetard;
            currHoldTime = min((int)((lastRPM - cfg.launchRPM) * cfg.limiterCut / 100.f), 200); // rpmError * gain and limit to 200 ms
            currRestore = (int)(cfg.limiterRetard / cfg.limiterDiv);
            cfg.fullCut = cfg.limiterFullCut;
            lastCut = currTime;
          }
          break;

        case PIT:
          if (cfg.limiterRPM && lastRPM > cfg.limiterRPM && !shiftingTrig)
          {
            shiftingTrig = true;
            limitingRPM = true;
            waitHyst = true;
            currRetard = cfg.limiterRetard;
            currHoldTime = min((int)((lastRPM - cfg.limiterRPM) * cfg.limiterCut / 100.f), 200); // rpmError * gain and limit to 200 ms
            currRestore = (int)(cfg.limiterRetard / cfg.limiterDiv);
            cfg.fullCut = cfg.limiterFullCut;
            lastCut = currTime;
          }
          break;

        case OFF:
          if (limitingRPM)
          {
            limitingRPM = false;
            shiftingTrig = false;
            cfg.fullCut = conf.getBool("fullCut");
          }
          break;
      }
    }

    if (lastRPM < cfg.minRPM)
      waitHyst = true;

    if (pressureValue > cfg.cutSens && lastRPM >= cfg.minRPM && !waitHyst && !shiftingTrig && !limitingRPM && (currTime - lastCut) >= cfg.deadTime*1000)
    {
      shiftingTrig = true;
      currRetard = map(lastRPM, cfg.minRPM, cfg.maxRPM, cfg.retardLow, cfg.retardHigh);
      currHoldTime = map(lastRPM, cfg.minRPM, cfg.maxRPM, cfg.holdTimeLow, cfg.holdTimeHigh);

      currRestore = (int)(currRetard / cfg.restore) + 1;

      waitHyst = true;

      // digitalWrite(GREEN_PIN, LOW); // On when shifting
      GPIO.out_w1tc = (1 << GREEN_PIN);

      lastCut = currTime;
    }

    if (shiftingTrig && (currTime - lastCut) >= currHoldTime*1000)
    {
      shiftingTrig = false;
      // digitalWrite(GREEN_PIN, HIGH); // Off
      GPIO.out_w1ts = (1 << GREEN_PIN);
    }

    lastCycle = currTime;
  }
}

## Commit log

2025-01-01 currently only 2 ch working, but no bugs found yet
    [code.ino]
2025-01-04 New Full cut option, 3 channels working now
    Full cut completely disables ignition pulses during the shift but keeps the smooth reactivation with retarded ignition.
    Currently only 3 channels usable because there aren't any timers left on the ESP32 S3. This should be fixable in the future but is not of high priority right now.
    [code.ino]
2025-01-31 added schematic + rpm limiter
2025-04-16 ESPNOW + limiter improved + gear sensing
2025-04-18 upload r3b files + code
    [bom_r3b.csv]
2025-08-02 Add R3b pnp file
    [pnp_r3b.csv]
2026-05-03 uploaded hall sensor files
    [magnet mount.step, sensor mount.step]
2026-05-03 updated pnp+bom files
    [bom_r3b.csv, bom_r3b.xlsx, pnp_r3b.csv]
